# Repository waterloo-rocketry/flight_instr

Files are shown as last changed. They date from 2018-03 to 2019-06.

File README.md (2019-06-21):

# flight_instr
This is the flight/engine instrumentation system used in Waterloo Rocketry's 2018 rocket, _Unexploded Ordnance (UXO)_. This repository tracks the hardware and software used in this system. The flight instrumentation PCB is a monolithic board containing an Arduino Nano, an SD card, a digital sensor suite, an analog sensor suite, a radio transceiver, and an H-bridge valve driver. Two copies of this board were used in UXO to successfully launch the rocket to 13000 ft.

This system is no longer in use. It has been replaced by RocketCAN, a collection of boards that implement the functionality of flight instrumentation in a modular manner. The new system is tracked in the `canhw`, `canlib`, and `cansw_*` repositories.

## Injector board assembly
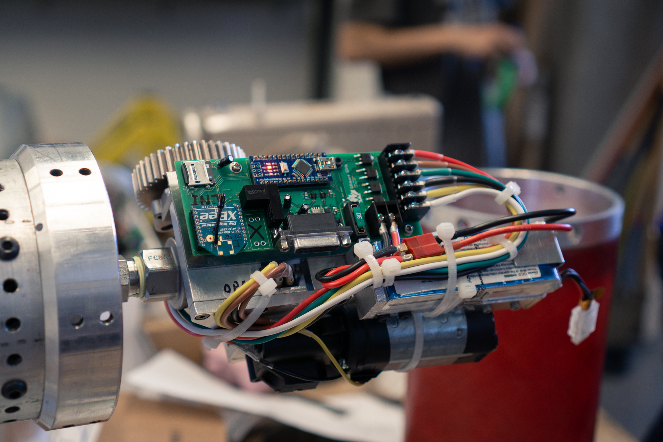
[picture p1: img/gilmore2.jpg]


## Vent board assembly
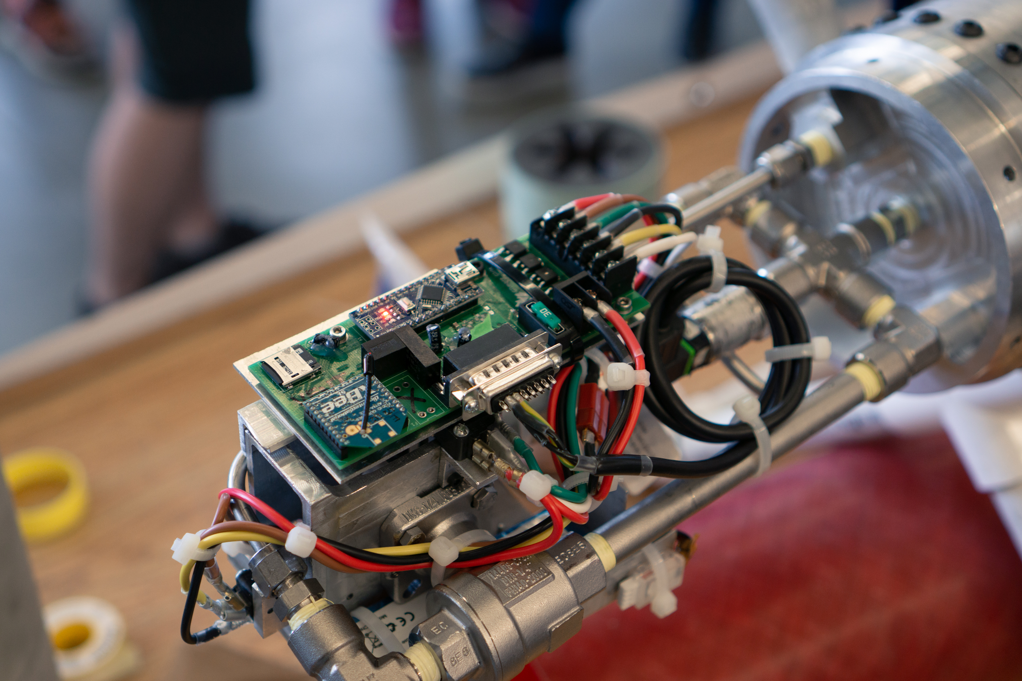
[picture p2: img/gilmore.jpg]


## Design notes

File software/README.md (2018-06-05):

### README ###

To build, run:

`make NODE=-DNODE_VENT` or `make NODE=-DNODE_INJ` depending on whether you want
to build the code for the board in the vent or injector section. One and only
one of these should be defined at all times. Make clean before switching
targets.

This changes the behaviour of the RLCS dependency and of some sensors.

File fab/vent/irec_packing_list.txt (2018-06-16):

Item                                        Quantity
-----------------------------------------------------------------------------
GG Vent                                     1
GG Vent Spare                               1
GG Injector                                 1
GG Injector Spare                           1
Xbee SC1                                    2
Pressure Sensors (TDH30)                    2
Sensor cables                               2       // thermistors attached
Lipo 2200mAh                                4
Microsd card                                2
USB Mini cable                              2
Spare arduino nano                          2

M3 Screw                                    8 min
Nylon screw (M3)                            4       // assuming there are already nylon screws in assembly
4-40 Screw                                  4 min

Ring conn                                   all
Quick conn                                  all
Limit switches                              all
Fuses 30A                                   3
Spare cable (16 AWG grey)                   5 ft

-----------------------------------------------------------------------------
Tool                                        Quantity
-----------------------------------------------------------------------------
Screwdriver (Phillips head)
Allen key (4-40)
Allen key (M3)
Tweezers

Crimpers/Strippers
Heat gun
Heat shrink

Soldering iron
Solder
Flux
Solder braid

Multimeter
Magnifying glass

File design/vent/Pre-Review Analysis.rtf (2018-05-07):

Pre-Review Analysis

Arduino:
- Arduino nano v3 clone.

Valve Section:
- Flyback diodes on H bridge? Currently using the body diodes of the MOSFET. Will add external flyback diodes if needed.
- Valve input is fused at 25A.
- PMOS high side switch: AOD417
- Max Id: -25A
- Max Vgs: +/-20V
- Vgs(th) between -1V and -3V
- Checked pinout: GDS
- NMOS low side switch: AOD476
- Max Id: 25A
- Max Vgs: +/-16V
- Vgs(th) between 0.6V and 2V
- Checked pinout: GDS
Both have TO252 packages.
All this should be fine to handle the maximum current going through that motor.

Xbee SC1:
- Decoupling capacitors: taken from data sheet.
- Input power supply should have a switching frequency greater than 500kHz, ripple less than 100mV (from datasheet).
- Current draw (idle): 50mA.

SD Card:
- Current consumption: write ~100mA
- Decoupling capacitor value (for power supply stability) from Altium blog general guidelines. Will refine.

- R-78E3.3-0.5: 500mA, 570kHz typ, 50mV ripple, 1.5mA quiescent current. Powers both Xbee and SD card.
- Xbee and SD card interfacing: UART and SPI respectively. Logic level is shifted from 3V3 to 5V through SN74LVC2T45. Data direction is from B to A when DIR is LOW. Capacitor values are based on data sheet application notes.

Analog Sensors:
- Thermistors: standard NTC, temperature range TODO
- Pressure sensor: TDH30 (solid state, 12-15V input, 0-5V output). Current consumption is approximately 7mA.
- SPU01 step-up regulator: input cap is internal. No value specified for output cap. Put in a conservative value that may be changed later.

Digital sensors:
- I2C logic level shifter MOSFET: DMG2302UK
- Vgs(th) between 0.3V and 1.0V
- Max Vsd: 1.2V
- 3.0 - 1.2 = 1.8 > max Vgs.
- Pinout checked to be GSD.
- Sensor circuits known to work after being tested on Gorgonzola.

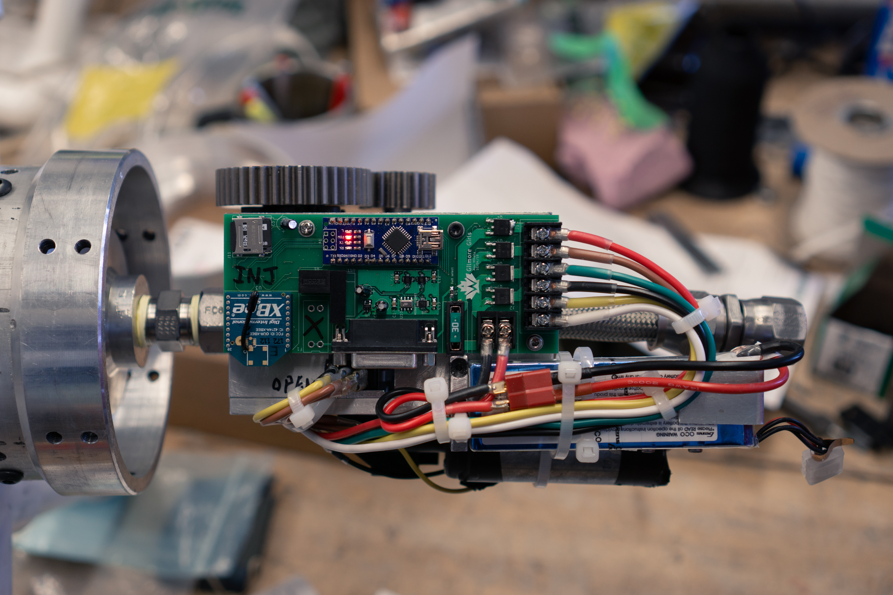
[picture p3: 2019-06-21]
img/gilmore3.jpg

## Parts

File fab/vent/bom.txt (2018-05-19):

Bill of Materials for vent section board
Based on git commit 7b35575

Toplevel stuff (arduino ignored)
---------------------------------------------------------------------
Fuse Holders        | 0891020.NXS       | 2                 | 36-3557-2-ND
battery block       | OSTYK22102030     | 1                 | ED2958-ND
LED                 | LTST-C171GKT      | 1                 | 160-1423-{1,2,6}-ND
=====================================================================
Valve Control Hierarchial sheet
---------------------------------------------------------------------
valve barrier       | OSTYK21106030     | 1                 | ED2938-ND
N-mos power         | AOD476            | 2                 | 785-1112-1-ND
P-mos power         | AOD417            | 2                 | 785-1106-1-ND
N-mos signal        | DMG2302UK         | 2                 | DMG2302UK-7DICT-ND
flyback diode       | BAS16GWJ          | 4                 | 1727-7320-1-ND
=====================================================================
Comms/logging Hierarchial sheet (Xbee ignored)
---------------------------------------------------------------------
3v3 regulator       | R-78E3.3-0.5      | 1                 | 945-1661-5-ND
Logic shifter       | SN74LVC2T45       | 3                 | 296-16845-1-ND
MicroSD             | 0472192001        | 1                 | WM6698CT-ND
Xbee socket header  | N/A               | 2                 | S5751-10-ND
=====================================================================
Sensors Analog Hierarchial sheet
---------------------------------------------------------------------
15v regulator       | SPU01M-15         | 1                 | 1866-4840-ND
DSUB conn           | A-DF 15 A/KG-T2S  | 1                 | AE10929-ND
=====================================================================
Sensors Digital Hierarchial sheet
---------------------------------------------------------------------
3v regulator        | LP2980AIM5-3.0    | 1                 | LP2980AIM5-3.0/NOPBCT-ND
I2C shifter mosfet  | DMG2302UK         | 2                 | DMG2302UK-7DICT-ND
3 axis gyro         | BMG250            | 1                 | 828-1065-1-ND
3 axis IMU          | LSM6DS3HTR        | 2                 | 497-16367-1-ND
Barometer/temp      | MS5607-02BA03     | 1                 | 223-1198-1-ND
=====================================================================
Passives - Resistors
---------------------------------------------------------------------
R1 - 0              | R2 - 100          | R3 - 100          | R4 - 10K
R5 - 10K            | R6 - N/A          | R7 - 10K          | R8 - 10K
R9 - 10K            | R10 - 10K         | R11 - 10K         | R12 - 10K
R13 - 10K           | R14 - 10K         | R15 - 10K         | R16 - 10K
R17 - 20K           | R18 - 20K         | R19 - 10K         | R20 - 270
R21 - 270           | R22 - 10K         | R23 - 10K         | R24 - 270
R25 - 270           | R26 - 10K         | R27 - therm       | R28 - therm
R29 - therm         | R30 - therm       | R31 - 10K         | R32 - 10K
---------------------------------------------------------------------
0    ohm            |                   | 1                 | RMCF0805ZT0R00CT-ND
100  ohm            |                   | 2                 | RMCF0805JT100RCT-ND
270  ohm            |                   | 4                 | RMCF0805JT270RCT-ND
10  Kohm            |                   | 18                | RMCF0805JT10K0CT-ND
20  Kohm            |                   | 2                 | RMCF0805JT20K0CT-ND
thermistor value    |                   | 4                 | 
=====================================================================
Passives - Capacitor
---------------------------------------------------------------------
C1 - 10u            | C2 - 10u          | C3 - 47u          | C4 - 10n
C5 - 10n            | C6 - 8.2p         | C7 - 1u           | C8 - 10n
C9 - 10n            | C10 - 10n         | C11 - 10n         | C12 - 100n
C13 - 100n          | C14 - 1u (Al)     | C15 - 2.2u(Al/Ta) | C16 - 100n
C17 - 100n          | C18 - 4.7u        |
---------------------------------------------------------------------
8.2 pF              |                   | 1                 | 1276-2697-1-ND
10  nF              |                   | 6                 | 1276-1078-1-ND
100 nF              |                   | 4                 | 478-10836-1-ND
1   uF              |                   | 1                 | 1276-6471-1-ND -> on hand
1   uF (Al)         |                   | 1                 | 		     -> on hand	
2.2 uF (Al/Ta)      |                   | 1                 |                -> on hand
4.7 uF              |                   | 1                 | 1276-2913-1-ND
10  uF              |                   | 2                 | 445-14420-1-ND
47  uF              |                   | 1                 |

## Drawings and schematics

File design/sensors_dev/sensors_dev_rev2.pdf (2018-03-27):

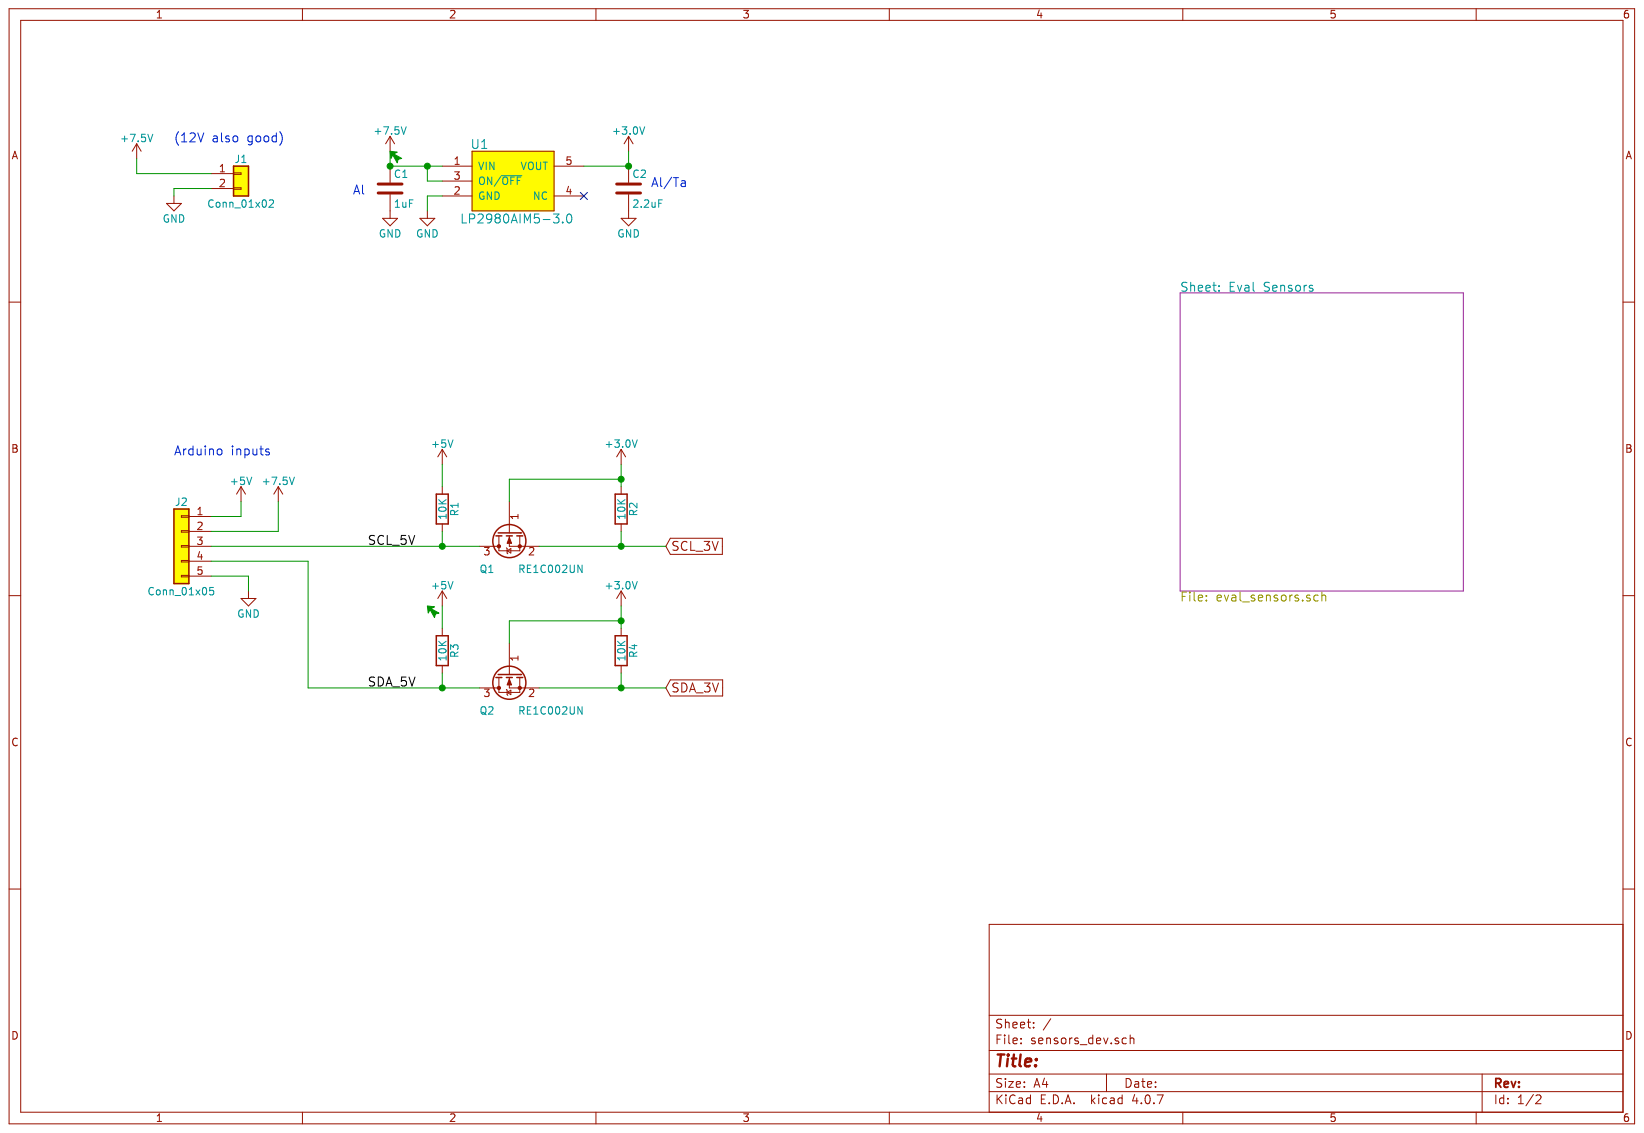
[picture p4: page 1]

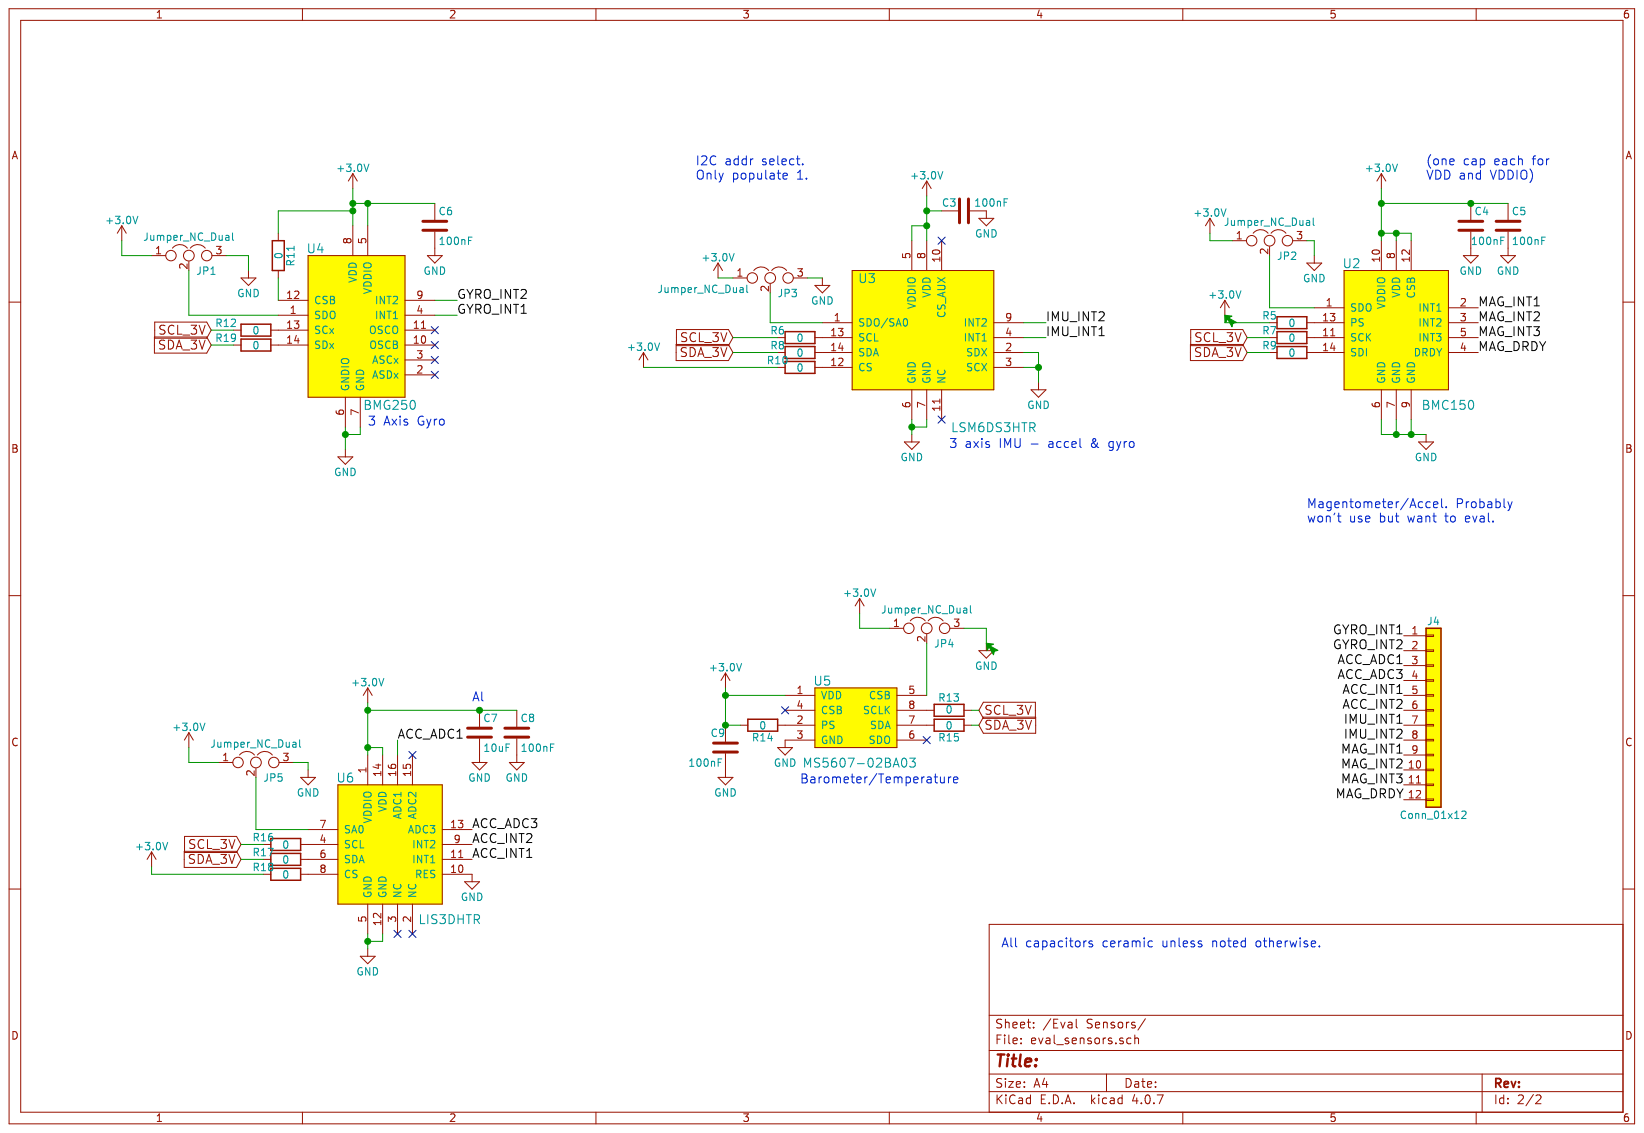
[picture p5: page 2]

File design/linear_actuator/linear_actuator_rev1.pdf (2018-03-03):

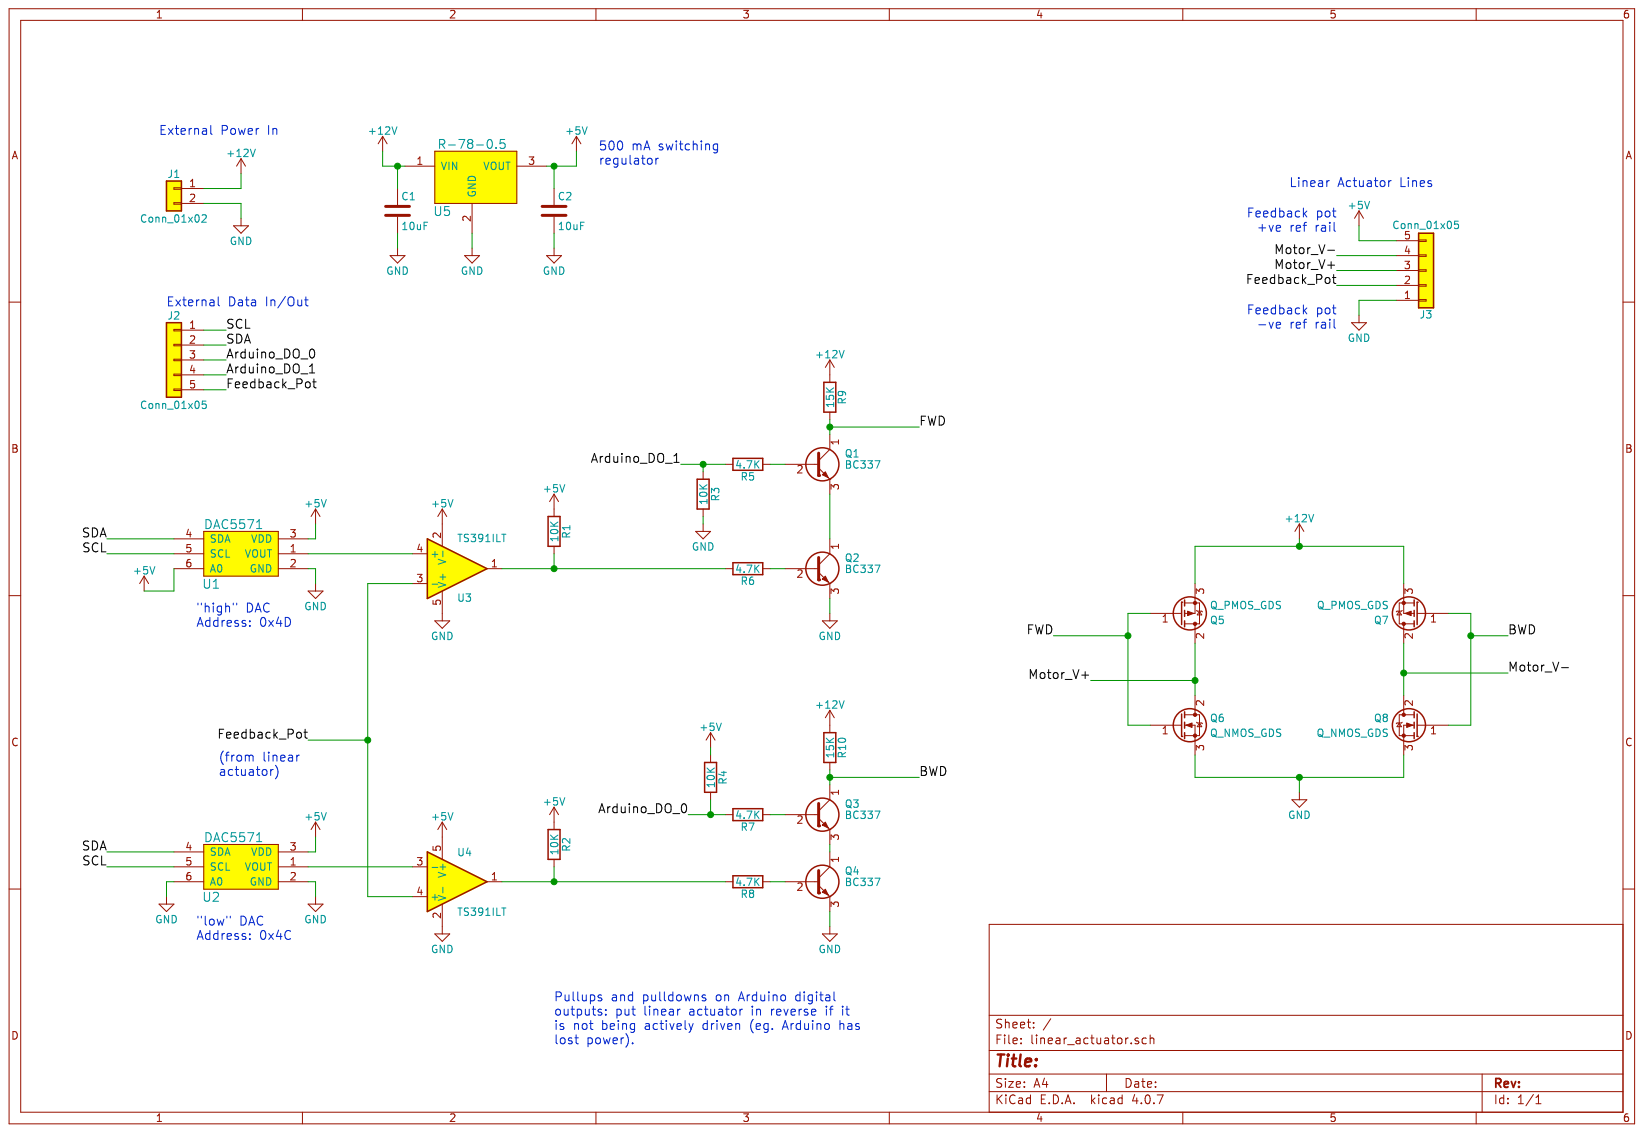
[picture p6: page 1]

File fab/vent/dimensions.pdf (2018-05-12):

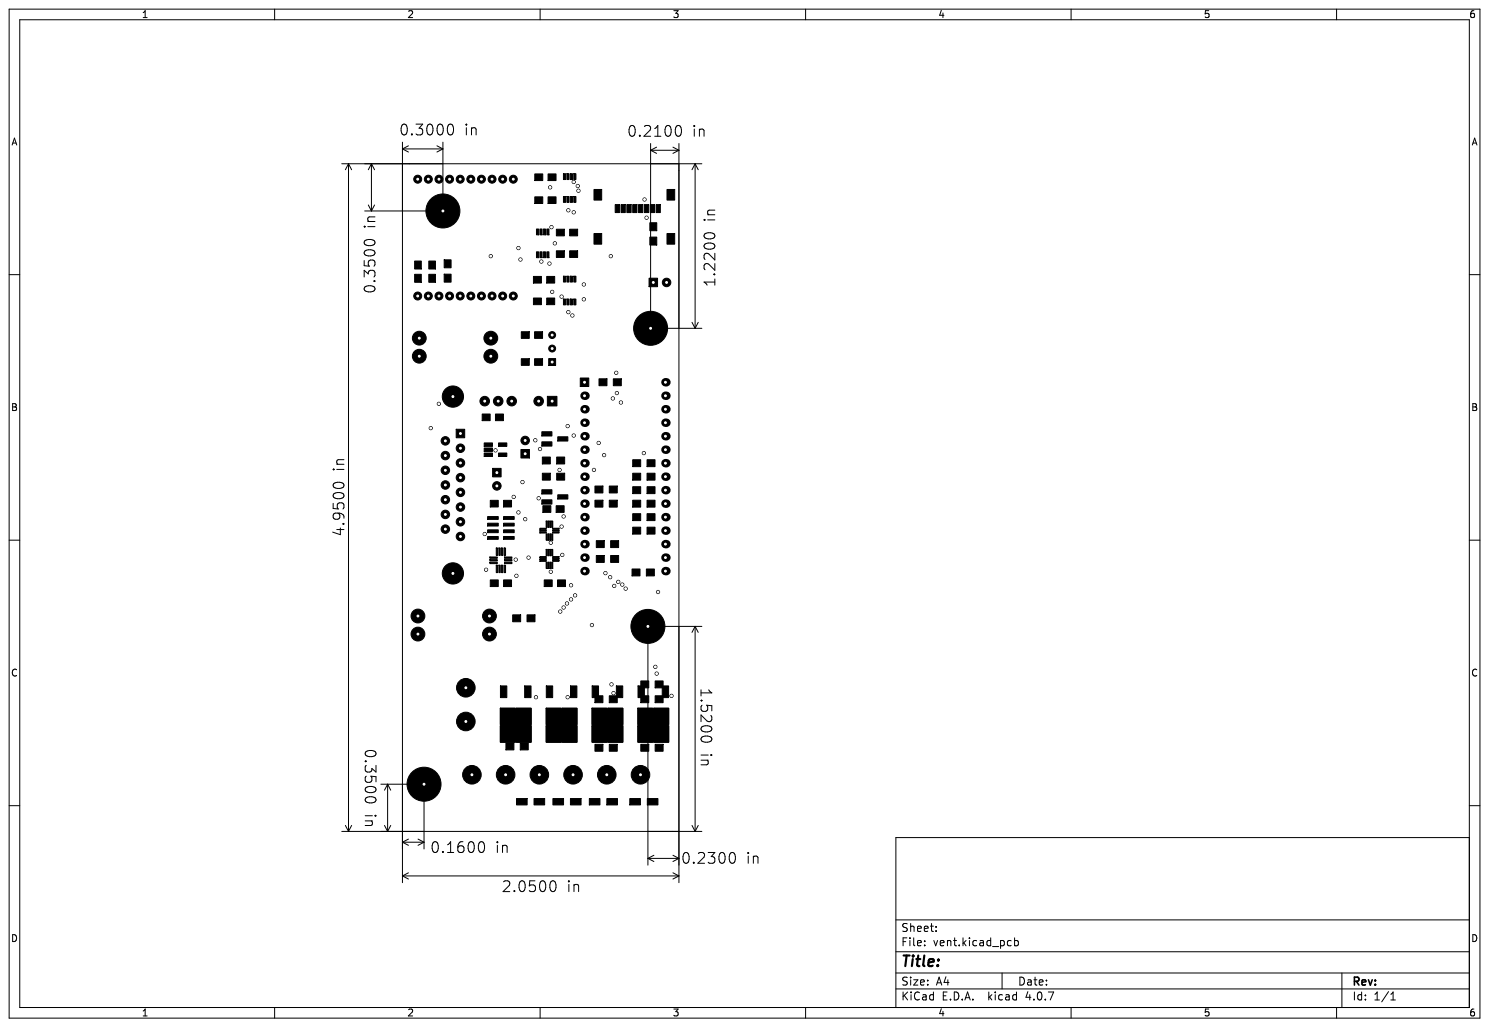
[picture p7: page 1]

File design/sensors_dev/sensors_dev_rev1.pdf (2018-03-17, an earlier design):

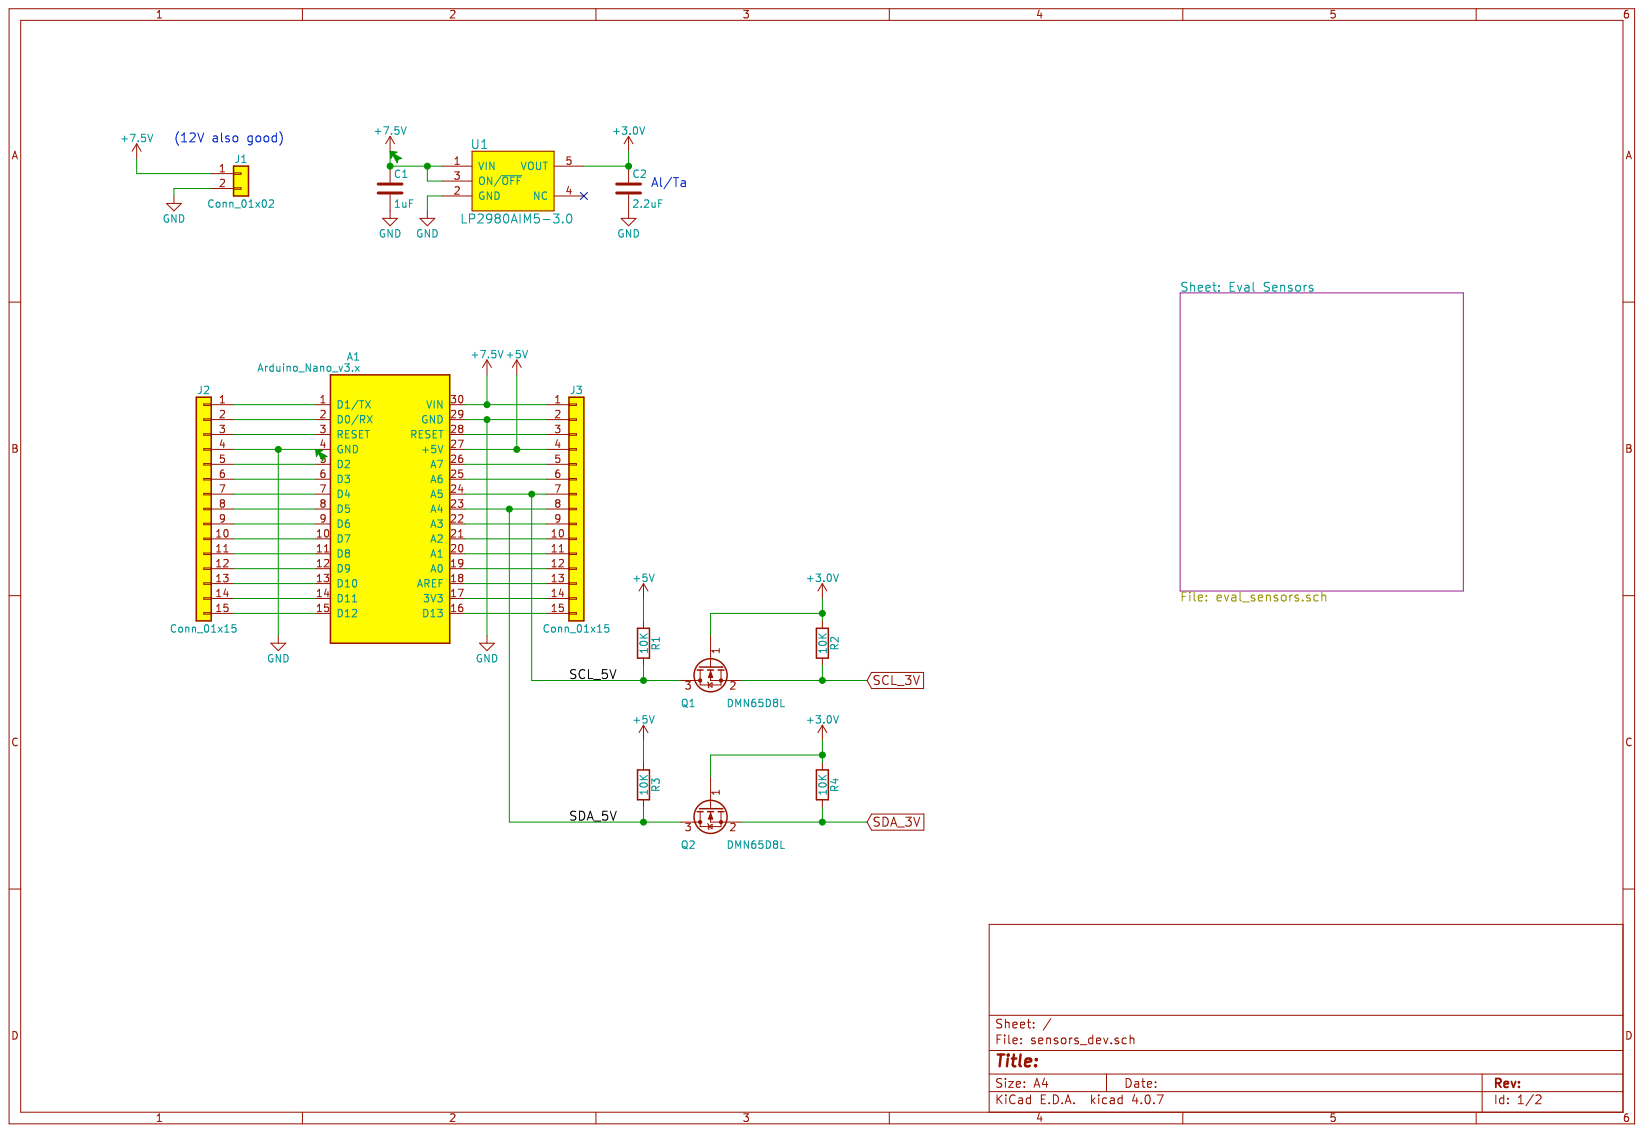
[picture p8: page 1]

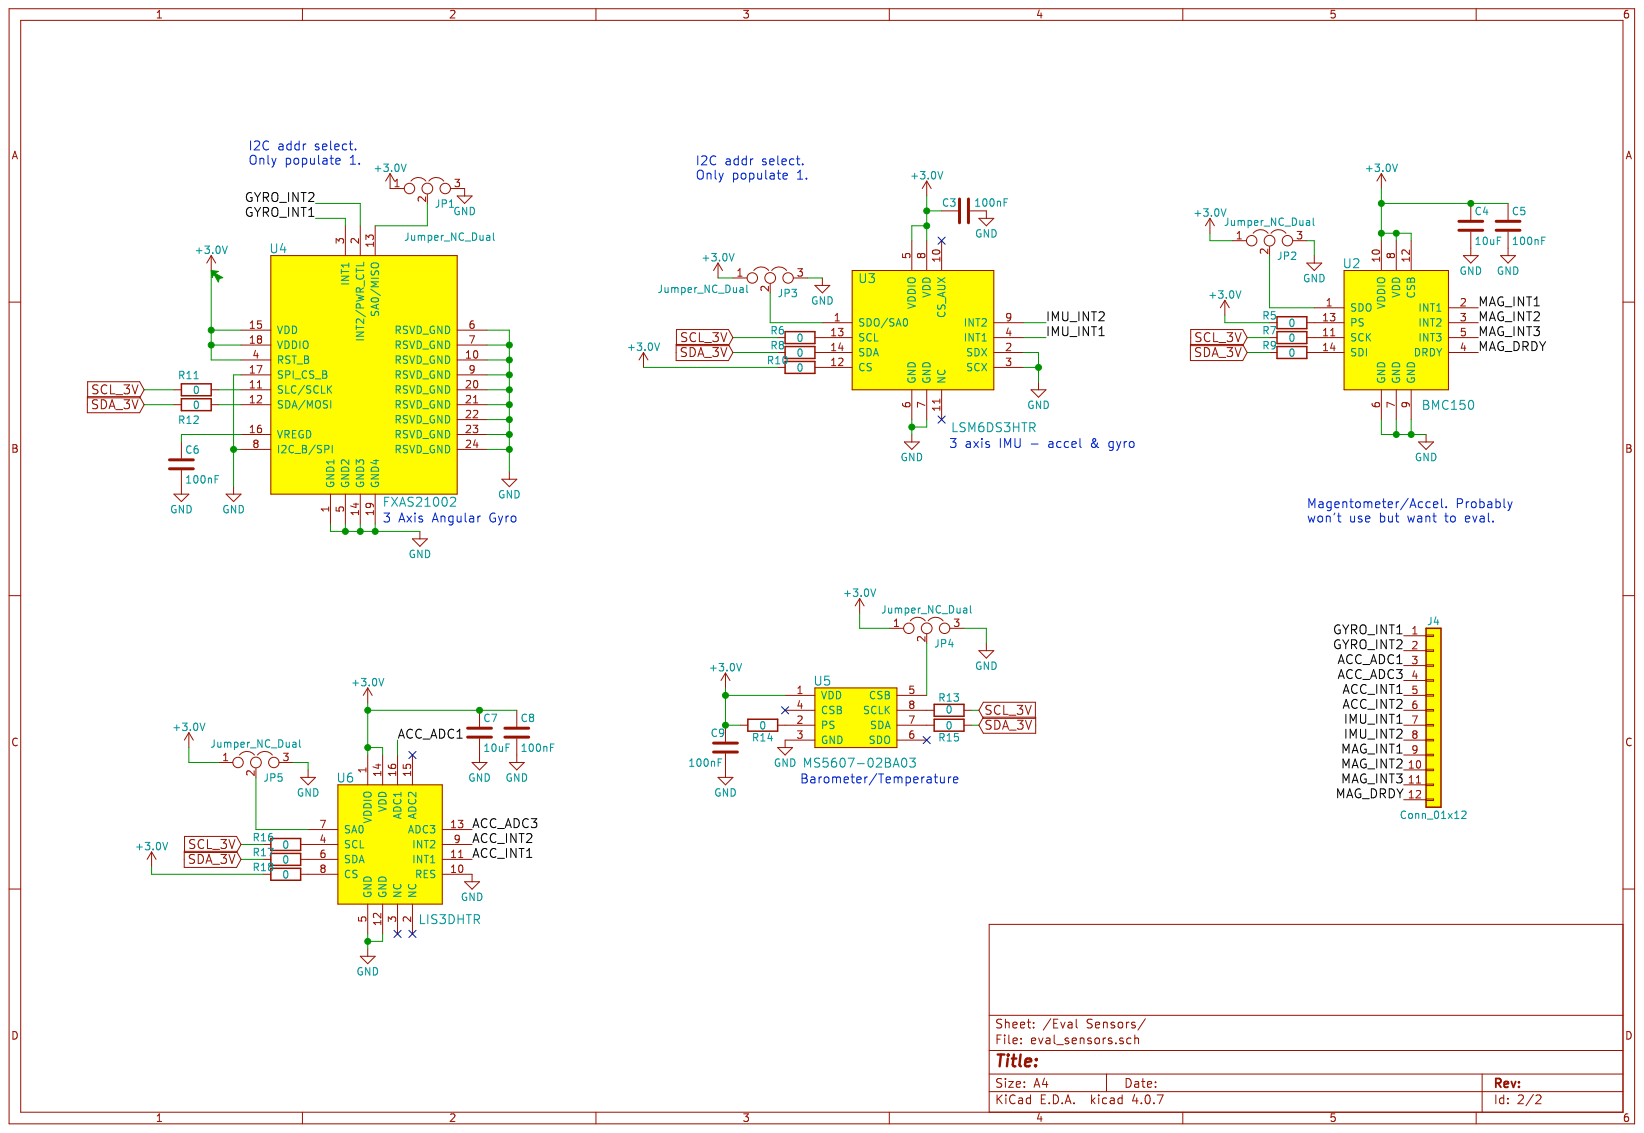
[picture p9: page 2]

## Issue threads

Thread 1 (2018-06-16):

No need to wait after Wire.requestFrom().

Koepel, 2018-06-16:
In the file "flight_instr/software/gyro.cpp", in the function "gyro_test_chipID()", the line "`while (!Wire.available());`" may be removed.
Explanation: [Common-mistakes#1](https://github.com/Koepel/How-to-use-the-Arduino-Wire-library/wiki/Common-mistakes#1)

amihaila, 2019-06-21:
Archiving repository, won't fix.

Closed 2019-06-21.

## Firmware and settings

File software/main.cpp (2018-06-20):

#include "Arduino.h"
#include "Wire.h"
#include "SPI.h"
#include "SD.h" 

#include "nodeio.ioio.h"
#include "IMU.h"
#include "gyro.h"
#include "MS5xxx.h"
#include "sdlogger.h"

#define OPEN_POS 2
#define CLOSE_POS 3
#define CLOSE_NEG 4
#define OPEN_NEG 5
#define LIMIT_OPEN 6
#define LIMIT_CLOSED 7

#define SD_CS 10

#define PRESSURE_PIN 6
#define THERM1 1
#define THERM2 2

#ifdef NODE_INJ
// P1
#define PRESSURE_SCALE (610.5 * 5 / 1024.0)
#define PRESSURE_ADD (-2.2)
#else
// P2
#define PRESSURE_SCALE (604 * 5 / 1024.0)
#define PRESSURE_ADD (-265)
#endif

#define SENSOR_SEND_INTERVAL 1000   // in milliseconds

// see LSM6DS3HTR datasheet
imu_t imu = {
    .imu_addr   = 0x6B,

    .odr_xl     = 0x07,     // 833 hz high performance mode
    .fs_xl      = 0x03,     // +/- 8g
    .odr_g      = 0x07,     // 833 Hz high performance mode
    .fs_g       = 0x03,     // 2000 dps

    .scale_xl   = XL_FS_16,
    .scale_g    = G_FS_2000
};

gyro_t gyro =  {
    .addr = 0x69,

    .gyr_bwp    = 0x2,      // normal mode
    .gyr_odr    = 0xc,      // 1.6 kHz
    .gyr_range  = 0x1,      // 1000 dps
    .scale      = 32.8      // associated to 1000 dps
};

MS5xxx baro(&Wire);          // tied to external library
float analogSensors[3];     // ox/cc pressure, temperature raw x2
sensor_data_t rlcs_data;    // data to be sent back to rlcs

// SD data file
extern File data_file;

int main() {
	init();
    
    Wire.begin();
    Serial.begin(9600);

    pinMode(SD_CS, OUTPUT);
    sd_init(SD_CS);
    sd_write_headers();

    nio_init(CLOSE_POS, CLOSE_NEG, OPEN_POS, OPEN_NEG);
    pinMode(LIMIT_OPEN, INPUT);
    pinMode(LIMIT_CLOSED, INPUT);

    imu_init(&imu);
    imu_whoami(&imu);

    gyro_init(&gyro);
    baro.connect();
    baro.ReadProm();
    
    long last_millis = 0;
    while (1) {
        nio_refresh();

        long timestamp = micros();
        imu_accel_read(&imu);
        imu_gyro_read(&imu);
        gyro_read(&gyro);
        float baro_pressure = baro.GetPres();
        float baro_temp = baro.GetTemp();

        analogSensors[0] = analogRead(PRESSURE_PIN) * PRESSURE_SCALE + PRESSURE_ADD;
        analogSensors[1] = analogRead(THERM1);
        analogSensors[2] = analogRead(THERM2);

        rlcs_data.pressure = analogSensors[0] > 0 ? analogSensors[0] : 0;
        rlcs_data.valve_limitswitch_open = !digitalRead(LIMIT_OPEN);
        rlcs_data.valve_limitswitch_closed = !digitalRead(LIMIT_CLOSED);
        
        if (millis() - last_millis > SENSOR_SEND_INTERVAL) {
            nio_send_sensor_data(&rlcs_data);
            last_millis = millis();
        }

        // snprintf is broken and life is hell
        float sensor_cluster_fuck[11] = {
            imu.accel_data[0], imu.accel_data[1], imu.accel_data[2],
            gyro.data[0], gyro.data[1], gyro.data[2], baro_pressure, baro_temp,
            analogSensors[0], analogSensors[1], analogSensors[2]
        };

        data_file.print(timestamp);
        for (int i = 0; i < sizeof(sensor_cluster_fuck) / sizeof(sensor_cluster_fuck[0]); i++) {
            data_file.print(", ");
            data_file.print(sensor_cluster_fuck[i]);
        }
        data_file.println();
        data_file.flush();
    }

    return 0;
}

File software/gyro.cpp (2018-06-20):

#include "Arduino.h"
#include "Wire.h"

#include "gyro.h"

int gyro_test_chipID(uint8_t addr) {
    Wire.beginTransmission(addr);
    Wire.write(GYRO_CHIPID_REG);
    Wire.endTransmission();

    Wire.requestFrom(addr, (uint8_t)1);
    uint8_t chipID = Wire.read();

    return (chipID == 0xd5 ? 0 : -1);
}

/*
 * Set gyro filter and sample rate parameters
 * gyr_bwp = 0x2 -> normal mode
 * gyr_odr = 0xC -> 1.6 kHz sample rate
 * See datasheet for other values
 *
 * Returns error code -> 0 on successful config
 */
uint8_t gyro_init(gyro_t *gyro) {
    // set power mode to normal
    Wire.beginTransmission(gyro->addr);
    Wire.write(GYRO_CMD_REG);
    Wire.write(0x15);
    Wire.endTransmission();
    delay(1);

    uint8_t gyro_config = gyro->gyr_bwp << 4 | gyro->gyr_odr;
    Wire.beginTransmission(gyro->addr);
    Wire.write(GYRO_CONFIG_REG);
    Wire.write(gyro_config);
    Wire.endTransmission();
    delay(1);

    Wire.beginTransmission(gyro->addr);
    Wire.write(GYRO_RANGE_REG);
    Wire.write(gyro->gyr_range);
    Wire.endTransmission();
    delay(1);

    // check that there are no errors
    Wire.beginTransmission(gyro->addr);
    Wire.write(GYRO_ERR_REG);
    Wire.endTransmission();

    Wire.requestFrom(gyro->addr, (uint8_t)1);
    uint8_t err_code = Wire.read();
    return err_code;
}

/*
 *  Perform fast offset calibration
 */
void gyro_calibrate(uint8_t addr) {
    // test - what are the current factors?
}

/*
 * Read x, y, z rates and temperature
 * Currently print them out to screen. Eventually just populate an array.
 */
void gyro_read(gyro_t *gyro) {
    // read gyroscopic data
    Wire.beginTransmission(gyro->addr);
    Wire.write(GYRO_DATA_BASE);
    Wire.endTransmission();

    uint8_t raw_readout[6] = {0};
    int i = 0;
    Wire.requestFrom(gyro->addr, (uint8_t)6);
    while (Wire.available()) {
        raw_readout[i++] = Wire.read();
    }

    // data is organized LSB first in 2's complement format
    gyro->data[0] = (int)((uint16_t)raw_readout[1] << 8 | raw_readout[0]) / gyro->scale;  // x rate
    gyro->data[1] = (int)((uint16_t)raw_readout[3] << 8 | raw_readout[2]) / gyro->scale;  // y rate
    gyro->data[2] = (int)((uint16_t)raw_readout[5] << 8 | raw_readout[4]) / gyro->scale;  // z rate

    // read temperature
    Wire.beginTransmission(gyro->addr);
    Wire.write(GYRO_TEMP_REG);
    Wire.endTransmission();

    i = 0;
    Wire.requestFrom(gyro->addr, (uint8_t)2);
    while (Wire.available()) {
        raw_readout[i++] = Wire.read();
    }
    uint16_t raw_temp = (uint16_t)raw_readout[1] << 8 + raw_readout[0];
    gyro->data[3]= (raw_temp / 512.0) + 23;
}

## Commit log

2018-03-03 Initial commit
    Linear actuator board schematic, sanity check software, and datasheets.
    [linear_actuator.kicad_pcb, linear_actuator.sch]
2018-03-09 Specify part numbers for the H bridge MOSFETS
    [linear_actuator.sch]
2018-03-17 First draft of sensor development board
    [eval_sensors.sch, sensors_dev.kicad_pcb, sensors_dev.sch]
2018-03-17 fix FXAS21002 protocol and bidir mosfets
    - Per review, tie pin 17 of FXAS21002 to HIGH the way it should be for
    I2C mode.
    - switch out bidirectional mosfets for some that would actually work.
    (VGS_th too hih relative to VDS for the old ones)
    [eval_sensors.sch, sensors_dev.sch]
2018-03-17 Add footprints and decoupling caps to some ICs
    [_saved_eval_sensors.sch, sensors_dev.sch]
2018-03-20 Start PCB and swap out gyro
    Old gyro (fxas) was 24 LGA and required a clearance between 3 and 4 mil,
    which increases costs and cuts down fab house options. Swapped out the
    gyro for another one with slightly higher drift but in a more convenient
    package (LGA14).
    [_saved_eval_sensors.sch, eval_sensors.sch, sensors_dev.sch]
2018-03-20 First draft PCB layout
    Todo: move arduino off board (use a breadboard instead). Will save a lot
    of space on the PCB and make the prototype cheaper.
    [sensors_dev.kicad_pcb]
2018-03-27 First pass board routing.
    Also, remove arduino from PCB since this is a dev board and there's no
    point paying for extra unused board space.
    [eval_sensors.sch, sensors_dev.kicad_pcb, sensors_dev.sch]
2018-03-29 Redo board placement and routing
    Will send to fab after final review.
    [eval_sensors.sch, sensors_dev.kicad_pcb, sensors_dev.sch]
2018-03-29 Minor review changes
    Move C9 and R14 further away from U5.
    [sensors_dev.kicad_pcb]
2018-05-01 Add dev board gerbers
    Requirements:
    5/5 mil trace/clearance
    [sensors_dev-B.Cu.gbl, sensors_dev-B.Mask.gbs, sensors_dev-Edge.Cuts.gm1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]
2018-05-01 Flight instr Injector/Vent schematic (1st Draft)
    Includes:
    - Arduino nano (rev3)
    - Xbee SC1
    - MicroSD card
    - Valve control
    - Analog sensors (thermistors & pressure)
    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
    [SD_card.sch, comms.sch, eval_sensors.sch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]
2018-05-04 Refine schematic
    - Add part numbers and correct pinout for mosfets
    - Add fuses to battery inputs
    - Add decoupling caps to logic translators
    - Add flyback diodes to H Bridge, to be populated if the body diodes of
    the mosfets are not sufficient.
    - Change H Bridge to operate with 4 inputs instead of 2.
    Also, misc directory cleanup.
    [SD_card.sch, comms.sch, sensors_analog.sch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]
2018-05-06 Review changes
    - Add debug LEDs
    - Add pullup resistors on logic shifters for xbee and sd card.
    - Add 0 ohm resistor between valve and control power sources (to allow
    for either one of both sources to be used).
    - Add another IMU
    - Add gate resistors to valve control mosfets
    [comms.sch, sensors_analog.sch, sensors_digital.sch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]
2018-05-06 Fix MOSFET gate resistors
    [sensors_analog.sch, valve_control.sch]
2018-05-07 Break out I2C lines on dsub connector
    [sensors_analog.sch, sensors_digital.sch, vent.sch]
2018-05-07 Add support for injector valve default state
    [sensors_analog.sch, valve_control.sch]
2018-05-08 Add connector part numbers to schematic
    [comms.sch, sensors_analog.sch, sensors_digital.sch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]
2018-05-08 Add barrier block footprints
    [sensors_analog.sch, valve_control.sch, vent.sch]
2018-05-08 Add MicroSD card socket PCB footprint
    Based on the datasheet drawing found at https://www.molex.com/pdm_docs/sd/472192001_sd.pdf
2018-05-08 Add more part numbers and footprints
    - Flyback diodes
    - Fuses
    - Xbee
    [comms.sch, sensors_analog.sch, sensors_digital.sch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]
2018-05-08 Add LED part numbers
    [vent.sch]
2018-05-09 Fix pullups/pulldowns for injector default
    [valve_control.sch]
2018-05-09 Create BOM
2018-05-09 Vent & Injector Board Layout
    [comms.sch, sensors_analog.sch, sensors_digital.sch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]
2018-05-10 Final vent/injector layout + routing
    [comms.sch, sensors_analog.sch, vent.kicad_pcb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]
2018-05-10 Add vent/injector gerbers
    [vent.drl, vent.gbl, vent.gbo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]
2018-05-10 Tweak 3V pour, regenerate gerbers
    [vent.kicad_pcb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]
2018-05-10 Update silkscreen, regen gerbers
    [vent.kicad_pcb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]
2018-05-12 Add solderpaste layer to Gerbers
    [vent.gtp]
2018-05-12 Add dimensions for Gilmore Girls
    [vent.kicad_pcb]
2018-05-19 Add valve wiring docs and BOM
    [diagrams.kicad_pcb, diagrams.sch]
2018-05-20 Kicad project cleanup
    - Remove backup files
    - Fix rescued components
    [vent.kicad_pcb]
2018-05-23 Add debug version of IMU driver
    Currently includes support for configuring and reading from the
    accelerometer and gyroscope. Debug version only: results are printed
    directly over serial.
    Cleanup to be done:
    - better handling of ord, fs, and other datasheet parameters
    - better organization of output data and whatnot
    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
2018-06-02 Correct pressure sensor calibration factors
    [main.cpp]
2018-06-10 Update IREC packing list
    - add radios, nylon screws, spare arduinos
    - remove dupont crimpers
2018-06-16 Add 3rd party barometer library
    Tested, it works. It might get swapped out for my own driver if I have
    time and feel like it. For now this is fine.
    [main.cpp]
2018-06-16 Debug version of BMG250 driver
    Implement proper configuration and readout. Still need to apply
    calibration offsets, choose proper ranges, and refactor into a better
    form.
2018-06-16 Clean up gyro code
2018-06-16 Make SD logging work
    Still full of debug printfs -> will need to remove these.
2018-06-16 Code cleanup
    - Clean up gyro and imu drivers.
    - Correct IMU address in main
    - Remove all the debug serial prints
    [IMU.cpp, gyro.cpp, main.cpp]
2018-06-20 Fix accel scaling and thermistor pin numbers
    [gyro.cpp, main.cpp]
2019-06-21 Add photos of PCBs
